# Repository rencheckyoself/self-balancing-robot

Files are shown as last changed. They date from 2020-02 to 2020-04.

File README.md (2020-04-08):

# Self Balancing Robot Project
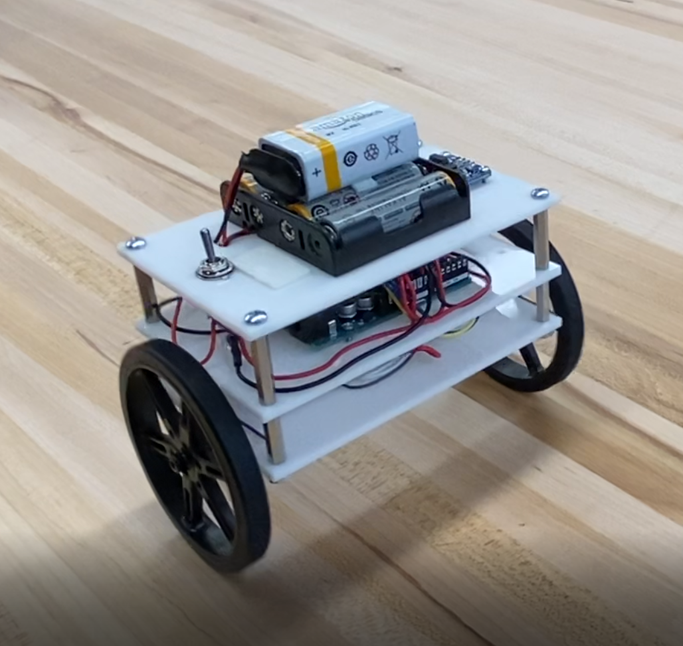
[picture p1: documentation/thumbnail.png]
thumbnail


This was a project to design and build a two-wheeled, self balancing robot that has a compact form factor. The challenge is that shorter the body design, the harder it is for the robot to easily maintain its balance. Since the feasibility of this system is not obvious, first the robot dynamics were solved and used to create a simulation of the system. This simulation was then used to inform the design and component selection process.

[Summary Video](https://www.youtube.com/watch?v=kY2ciNZqLZk)

This repository contains:
- A python script to the dynamics of the system and determine the equations of motion
- A ROS package that uses the equations of motion to simulate the self balancing robot
- Design files and BOM of the robot
- Arduino script to control the robot.

## How to use this repo:

If you want to use this repository to design your own self balancing robot or just recreate the iteration shown above, follow these steps:

**1) Run the  file `SelfBalancing_AllSymbolic.py`.**

Requires: python3, sympy, numpy, scipy, and pickle

This file will symbolically solve the Euler-Lagrange equations to derive the equations of motion that characterize a two wheeled, self balancing robot. This will generate a set of pickle files that are used to transfer the equations to the ROS simulation. This file takes about **30 min to fully run** due to the amount of symbols being processed, but your mileage may vary. If you would like to see the actual solutions, the raw Latex code is in the 'solutions.txt' file or you can run the `print_solutions.py` file.

See [derivations.pdf](documentation/derivations.pdf) in the documentation folder for more information on the system setup and derivation of the equations.

**2) Simulate the robot by launching `self_balance.launch`**

Requires: ROS Melodic

This will launch the simulation using the default settings used for the design files in this repo. Once loaded, call the `/start` service to start the simulation. You will need to update the `file_path_params.yaml` in the `simulate` node to update the locations of where to find pickle files you generated earlier.

Package Desciption:
  - `dynamics`: This package contains all of the files relevant to the computational component of the simulation. The `simulate` node uses an RK4 integration method combined with the symbolic equations of motion to compute the robot state for every time step. The robot state is then fed into a PID control scheme to compute the required motor torque to keep the robot upright following this control scheme shown below.

    - If you would like to customize the simulation to your own parameters, modify the `robot_params.yaml` file to simulate a different robot configuration. These parameters are best pulled from CAD files, see the included CAD mass properties images in the documentation directory for an example.

    - To modify the controller gains, change the values in the `controller_param.yaml` file.
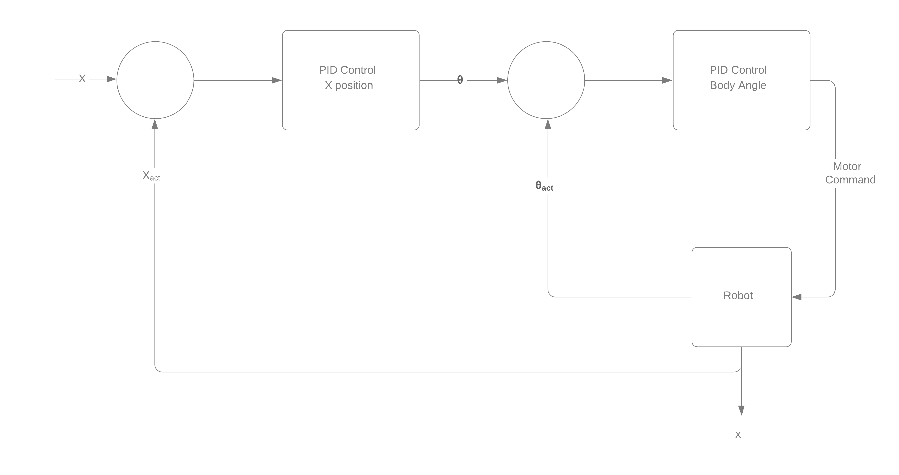
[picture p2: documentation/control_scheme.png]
ControlScheme
     

- `visualization`: This package contains all of the files relevant to the visual component of the simulation. The included launch file displays the `balance_bot.urdf.xacro` and is useful if you want to modify the existing model.

    - To use your own mesh, save an STL for your wheel and an STL for the robot body assembly and place them in the `meshes` directory. Either call your files the same name or update the file names inside of `balance_bot.urdf.xacro` to match your files.

**3) Build it!**

The files located in the `Prototyping` directory should be everything you need to build your own or use the insights discussed below to make your own modifications.

It contains:
 - CAD files
 - PDFs for laser cutting
 - Bill of materials
 - Wiring Diagram (shown below)
 - Arduino Source Code:   
 Required libraries:
 Adafruit BNO055,
 Adafruit Unified Sensor,
 EnableInterrupt by Mike Schwager,
 PID by Brett Beauregard,
 QuadratureEncoder by Cheng Saetern

There is an extra svg file called `motorSpacer.svg` that is meant for laser cutting an extra part not currently in the CAD. This piece goes between the motor and the bottom plate so that the encoder wires do not pinch the rotating magnet and stall the motors.

Currently the code does not actually incorporate the encoders to accomplish the position control component of the simulation.

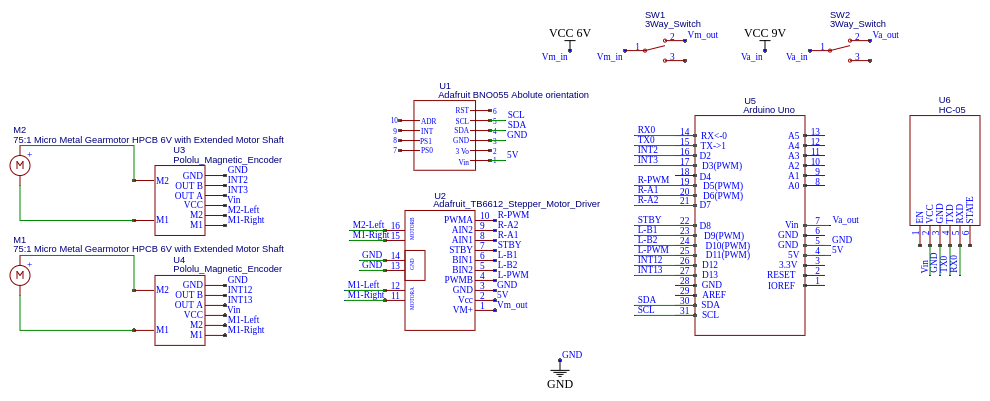
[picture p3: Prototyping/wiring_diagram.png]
WiringDiagram


## Lessons Learned

V2 is currently in-progress and the design will be largely the same but incorporating the changes based on the following insights:

1) The actual V1 build came out much heavier than anticipated, this can be attributed to not accounting for the components not in CAD (wires, nuts, screws, etc.) and the 9V battery. This was added late due to the 6V AA pack not being able to reliably power both the Arduino and the motors. 

2) The torques and speeds required for this design, are pushing these motors to their design limits. Therefore, any drop below their rated operating voltage of 6V really hurts their ability to output the required control.

3) The IMU used has onboard processing that provides easy access to an absolute position. Since the system is oscillating very quickly the 100Hz data stream may not be quick enough for to allow the motors enough time to react.

4) the IMU fell out of calibration after a few tests and caused the robot to try and balance to a non-vertical position.

5) There is some play in the wheel shaft to the gear box that allows the body to rotate a couple degrees without the motors spinning. Since the window of stable positions is only +/-6 degrees or so, this amount of play is not negligible.

Potential Solutions for V2:
 - Switch to aluminum standoff to save weight
 - Switch to an Arduino Nano and remove middle plate to save weight
 - Switch to 2S Lipo battery to save weight
 - integrate a 6V DC-DC regulator to power the motors
 - Incorporating encoder-based position control can help counteract the IMU calibration issues
 - Simulate V2 design a reevaluate motor selection based on required torques and wheel speeds
 - Slight increase of the body height to make the balancing easier and allow the control system more time to react.

## Future Plans

This repository is for an active project and a lot of insight was drawn from the first design.

Planned items:

- Integrate simulation functionality for different torques applied to each wheel. This will enable the simulation to turn and eventually follow waypoints.
- Construct a V2 robot that will be able to balance unteathered.
- Incorporate encoders into the V2 control scheme
- Control the physical robot to follow a set of waypoints in 3D space

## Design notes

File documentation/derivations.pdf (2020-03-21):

# Self Balancing Robot Derivations

### Michael Rencheck

### March 21, 2020

## 1 Problem Set Up

To solve the Euler-Lagrange equations, it is best to first define the frames and state vector that describe the problem and identify the transformations needed:

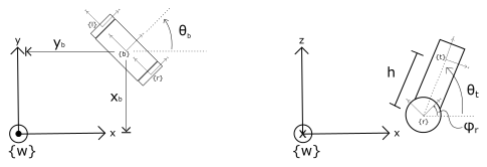
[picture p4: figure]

Figure 1: The frames used for the derivation

Frames:

w: world frame
b: robot base frame - centered between the wheels on the axis of rotation r: right wheel frame - centered on the wheel
l: left wheel frame - centered on the wheel
t: center of mass frame - located line with the base frame

Parameters:

xb: robot x-position
yb: robot y-position
θb: robot heading angle
θt
: robot body angle
φr: right wheel angle
φl

: left wheel angle
r: wheel radius
ht

: distance from rotation point to the center of mass D: distance between the two wheels

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

Find the kinetic energy of each link:

KEtot = KEr + KEl + KEt

KEr =

1
2

∗ Vr

T
∗ Gwheel ∗ Vr

KEl =

1
2

∗ Vl

T
∗ Gwheel ∗ Vl

KEt =

1
2

∗ Vt

T
∗ Gbody ∗ Vt

Where:
V: is a 6Vector twist
G: is a spatial inertia matrix
m: is mass of the respective body
I: is the moment of inertia about a principle axis

Vx = T

−1

wx ∗ T˙
wx

Gx =

mx | 0 | 0 | 0 | 0 | 0
0 | mx | 0 | 0 | 0 | 0
0 | 0 | mx | 0 | 0 | 0
0 | 0 | 0 | Ixx | 0 | 0
0 | 0 | 0 | 0 | Iyy | 0
0 | 0 | 0 | 0 | 0 | Izz

Find the Potential Energy of each link:

P Etot = P Er + P El + P Et

P Er = 0

P El = 0

P Et = (mtgh)sin(θt)

Define the constraint equations¹ :

λ =

"
λ1
λ2

∇φ =

"
1 0 0 r ∗ cos(θb) r ∗ cos(θb) 0

0 1 0 r ∗ sin(θb) r ∗ sin(θb) 0#

Last define the external force vector:

1For more details, see Robotic Manipulation, Murry, Li, Sastry pg. 272

Fext =

0
0
0

τmotor

τmotor
0

Finally solve the systems of equations for q¨ and λ:

dL
dq˙

−

dL
dq = Fext + λ∇φ

φ¨ =

d
dt(∇φ ∗ q˙)

See the included txt for the raw latex code of the solutions. This output was generated using the included python code.

A couple notation changes in the txt file: subscript w: wheel subscript b: body t variables: θ p variables: φ
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

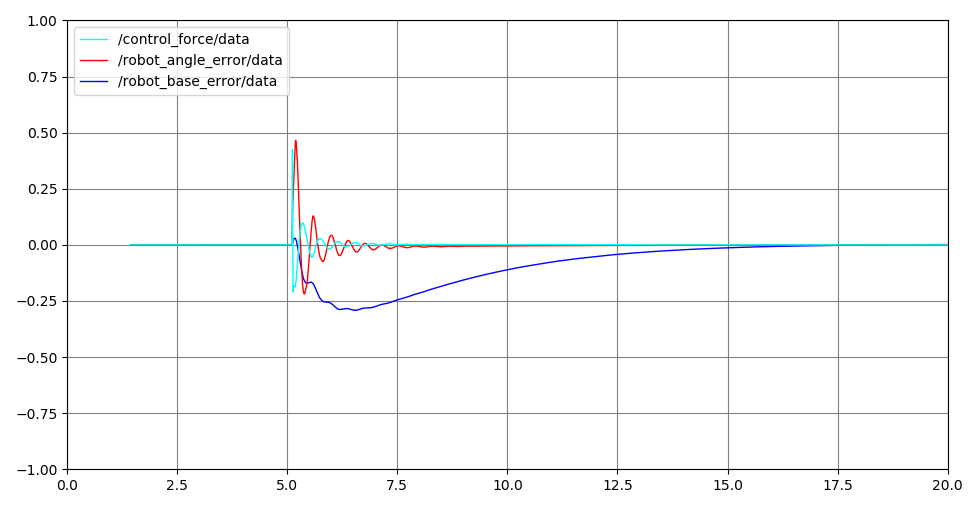
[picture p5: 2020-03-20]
documentation/simulatiuonresults.png

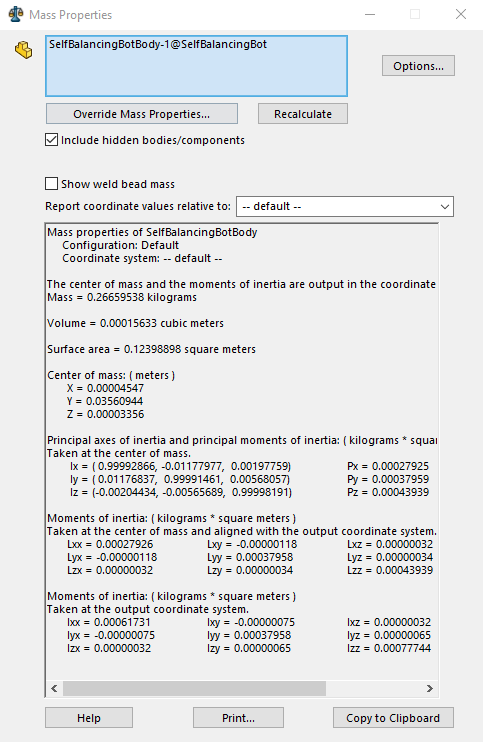
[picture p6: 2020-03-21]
documentation/V1 Body Properties.png

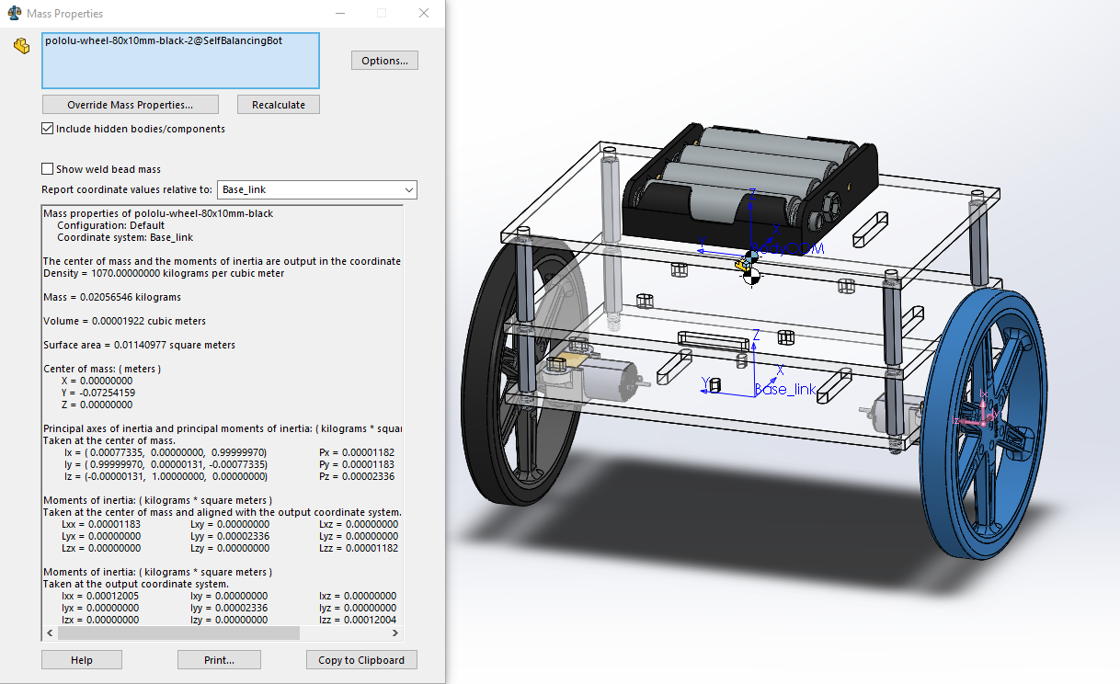
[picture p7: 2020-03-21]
documentation/WheelInertia.png

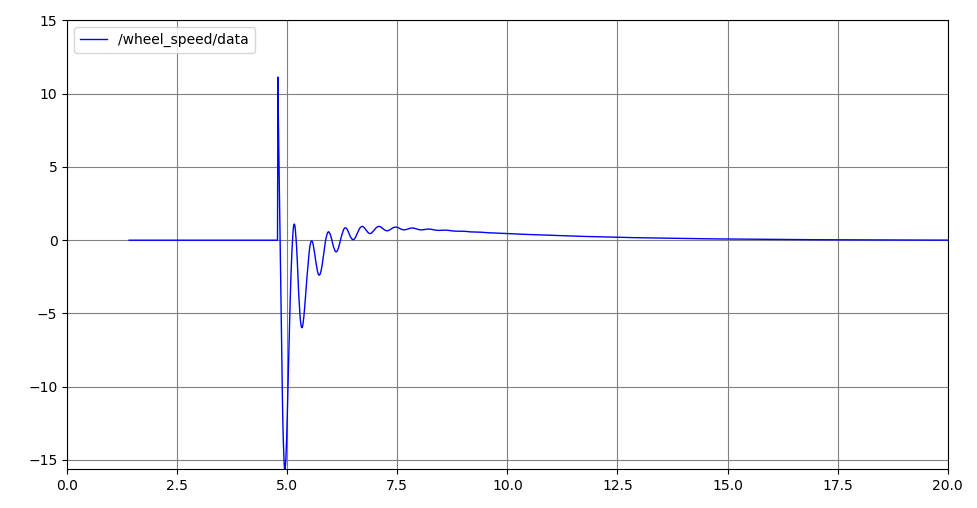
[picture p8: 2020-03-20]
documentation/wheel_speed.png

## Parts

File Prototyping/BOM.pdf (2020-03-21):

| Link | Quantity
Body | 1/8" Acryllic
Motors | https://www.pololu.com/product/3074 | 2
Motor Mount | https://www.pololu.com/product/989 | 2
Wheels | https://www.pololu.com/product/1430 | 2
Motor Driver | https://www.adafruit.com/product/2448 | 1
Encoders | https://www.pololu.com/product/3081 | 2
IMU | https://www.adafruit.com/product/2472 | 1
AA Battery Holder https://www.amazon.com/LAMPVPATH-Battery-Holder-Leads-Wires/dp/B07T7MTRZX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 1
9V Battery Connectorhttps://www.amazon.com/BBTO-Battery-Connector-Cable-Connection/dp/B0779ZSNS3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 1
Toggle Switch | https://www.amazon.com/yueton-Terminals-Position-Toggle-Switch/dp/B013DZB6CO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 1
Arduino Uno | https://www.amazon.com/ARDUINO-A000073-ATMEGA328-Original-Version/dp/B007R9TUJE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 1
Standoffs | https://www.mcmaster.com/91075a117 | 4
Standoffs | https://www.mcmaster.com/91075a115 | 4
Screws | #2/56 for PCBs & #6/32 | Various
Nuts | #2/56 for PCBs & #6/32 | Various
Lock Washers | #2/56 for PCBs & #6/32 | Various

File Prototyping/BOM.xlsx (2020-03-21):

 | Link | Quantity | Notes
Body | 1/8" Acryllic
Motors | https://www.pololu.com/product/3074 | 2
Motor Mount | https://www.pololu.com/product/989 | 2
Wheels | https://www.pololu.com/product/1430 | 2
Motor Driver | https://www.adafruit.com/product/2448 | 1 | PWM for velocity control
Encoders | https://www.pololu.com/product/3081 | 2
IMU | https://www.adafruit.com/product/2472 | 1 | May not be needed if the camera has the IMU
AA Battery Holder | https://www.amazon.com/LAMPVPATH-Battery-Holder-Leads-Wires/dp/B07T7MTRZX | 1
9V Battery Connector | https://www.amazon.com/BBTO-Battery-Connector-Cable-Connection/dp/B0779ZSNS3?s=industrial | 1
Toggle Switch | https://www.amazon.com/yueton-Terminals-Position-Toggle-Switch/dp/B013DZB6CO?s=industrial | 1
Arduino Uno | https://www.amazon.com/ARDUINO-A000073-ATMEGA328-Original-Version/dp/B007R9TUJE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 | 1
Standoffs | https://www.mcmaster.com/91075a117 | 4
Standoffs | https://www.mcmaster.com/91075a115 | 4
Screws | #2/56 for PCBs & #6/32 | Various
Nuts | #2/56 for PCBs & #6/32 | Various
Lock Washers | #2/56 for PCBs & #6/32 | Various

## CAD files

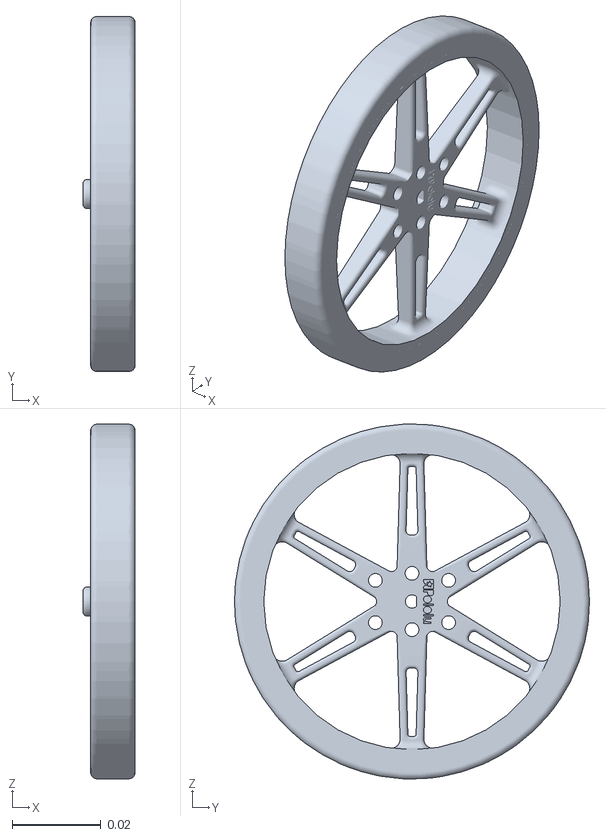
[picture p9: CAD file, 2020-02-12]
src/visualization/meshes/Wheel.STL
0.0117 x 0.08 x 0.0799

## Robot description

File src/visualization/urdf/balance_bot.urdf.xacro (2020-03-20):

<?xml version="1.0"?>
<robot xmlns:xacro="http://www.ros.org/wiki/xacro" name="balance_bot">


  <!-- Load in parameters from the YAML file -->
  <xacro:property name="props" value="${load_yaml('$(find dynamics)/config/robot_params.yaml')}"/>

  <xacro:property name="wheel_radius" value="${props['wheel_radius']}"/>
  <xacro:property name="wheel_base" value="${props['body_wheel_base']}"/>

  <xacro:property name="body_width" value="${props['body_width']}"/>
  <xacro:property name="body_height" value="${props['body_height']}"/>
  <xacro:property name="body_thickness" value="${props['body_thickness']}"/>
  <xacro:property name="body_com_height" value="${props['body_com_height']}"/>

  <xacro:property name="motor_height" value="0.0115"/> <!-- distance between wheel rotation axis and bottom plate-->
  <xacro:property name="mid_tier" value="0.0191"/> <!-- distance between mid plate and bottom plate-->
  <xacro:property name="top_tier" value="0.0254"/> <!-- distance between mid plate and top plate-->
  <xacro:property name="motor_shaft" value="0.00907"/> <!-- length of the motor_shaft -->

  <material name="smokey">
    <color rgba=".1 .1 .1 1"/>
  </material>

  <material name="wheel">
    <color rgba=".5 .5 .5 .5"/>
  </material>

  <material name="invisible">
    <color rgba="0 0 0 0"/>
  </material>

  <!-- Macro to load a part with a mesh -->
  <xacro:macro name="body_link_mesh" params="name lxyz lrpy mat meshfile meshscale jxyz jrpy">
    <link name="${name}">
      <visual>
        <origin rpy="${lrpy}" xyz="${lxyz}" />
        <geometry>
          <mesh filename="${meshfile}" scale="${meshscale}"/>
        </geometry>
        <material name="${mat}"/>
      </visual>
    </link>

    <joint name= "${name}_joint" type="fixed">
      <origin xyz="${jxyz}" rpy="${jrpy}" />
      <parent link="moving_link"/>
      <child link="${name}" />
    </joint>
  </xacro:macro>

  <xacro:macro name="wheel_link_mesh" params="name lxyz lrpy mat meshfile meshscale jxyz jrpy">
    <link name="${name}">
      <visual>
        <origin rpy="${lrpy}" xyz="${lxyz}" />
        <geometry>
          <mesh filename="${meshfile}" scale="${meshscale}"/>
        </geometry>
        <material name="${mat}"/>
      </visual>
    </link>

    <joint name= "${name}_axle" type="continuous">
      <origin xyz="${jxyz}" rpy="${jrpy}" />
      <parent link="base_link"/>
      <child link="${name}" />
      <axis xyz = "0 -1 0"/>
    </joint>
  </xacro:macro>

  <!-- The base link of the robot center between the two wheels directly below the COM of the body -->
  <link name="base_link" >
    <visual>
      <geometry>
        <sphere radius=".0025" />
      </geometry>
      <material name="black">
        <color rgba="0 0 0 1" />
      </material>
      <origin rpy="0 0 0" xyz="0 0 ${wheel_radius}"/>
    </visual>
  </link>

  <link name="moving_link">
    <visual>
      <geometry>
        <sphere radius=".0025" />
      </geometry>
      <material name="black"/>
      <origin xyz="0 0 ${body_com_height}" rpy="0 0 0"/>
    </visual>
  </link>

  <joint name="body_joint" type="continuous">
    <origin xyz="0 0 ${wheel_radius}" rpy="0 ${-pi/2} ${pi}" />
    <parent link="base_link"/>
    <child link="moving_link" />
    <axis xyz="0 1 0"/>
  </joint>

  <xacro:body_link_mesh name="body_mesh" mat="smokey" lxyz="${-body_thickness/2} ${-body_width/2 - motor_shaft} ${-motor_height/2}" lrpy="0 0 0" meshfile="package://visualization/meshes/SelfBalancingBotBody.STL" meshscale="1 1 1" jxyz="0 0 0" jrpy="0 0 0"/>

  <xacro:wheel_link_mesh name="left_wheel" mat="wheel" lxyz="${wheel_radius} ${body_width/2} ${-wheel_radius}" lrpy="0 0 ${pi/2}" meshfile="package://visualization/meshes/Wheel.STL" meshscale="1 1 1" jxyz="0 0 ${wheel_radius}" jrpy="0 0 0"/>

  <xacro:wheel_link_mesh name="right_wheel" mat="wheel" lxyz="${-wheel_radius} ${-(body_width/2)} ${-wheel_radius}" lrpy="0 0 ${-pi/2}" meshfile="package://visualization/meshes/Wheel.STL" meshscale="1 1 1" jxyz="0 0 ${wheel_radius}" jrpy="0 0 0"/>

</robot>

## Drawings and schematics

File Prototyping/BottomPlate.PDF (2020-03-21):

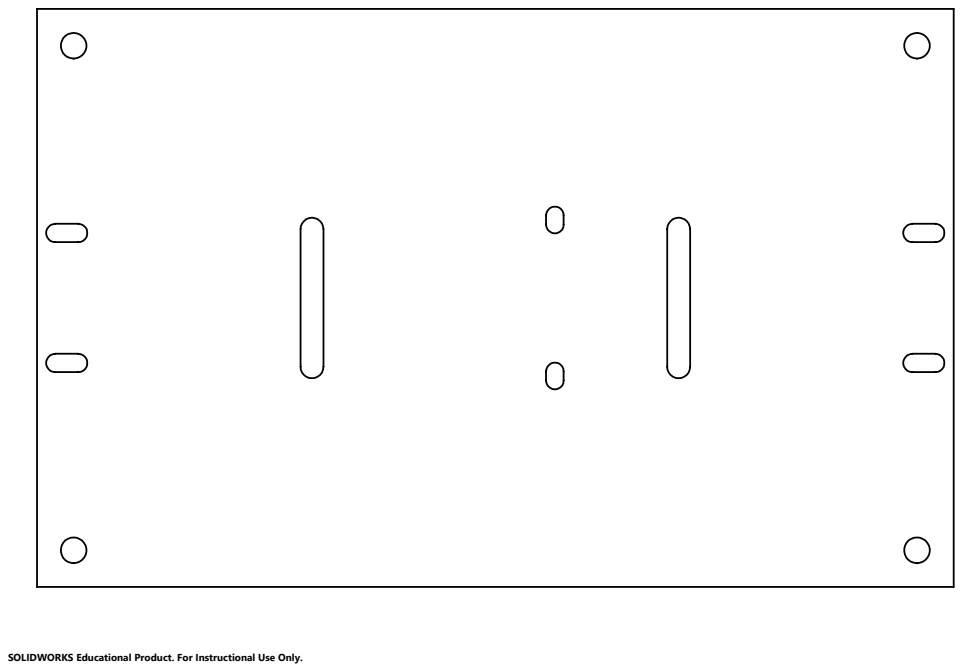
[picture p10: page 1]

SOLIDWORKS Educational Product. For Instructional Use Only.

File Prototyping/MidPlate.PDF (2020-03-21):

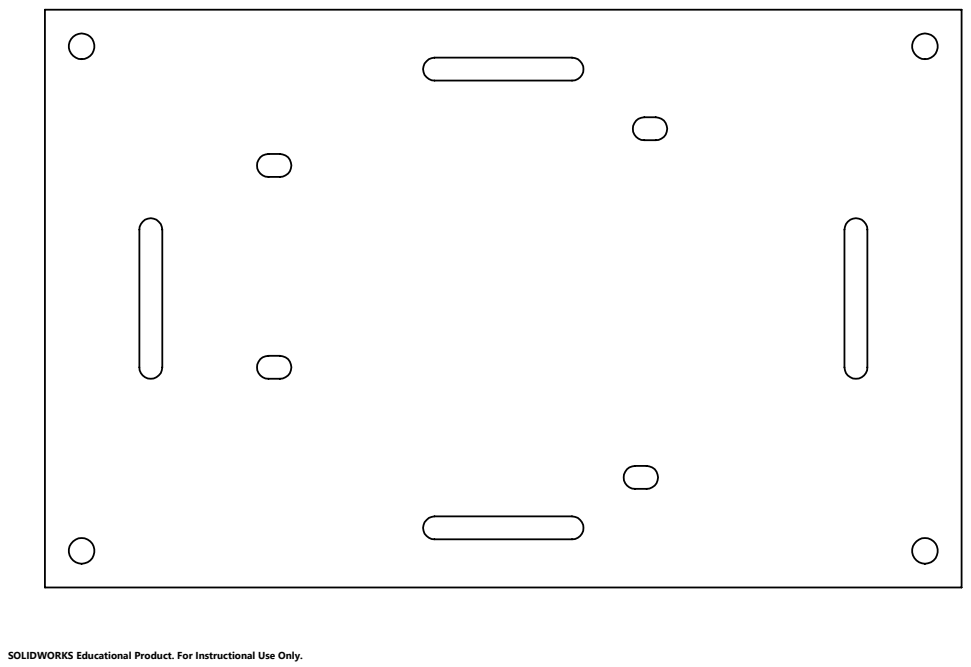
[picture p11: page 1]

SOLIDWORKS Educational Product. For Instructional Use Only.

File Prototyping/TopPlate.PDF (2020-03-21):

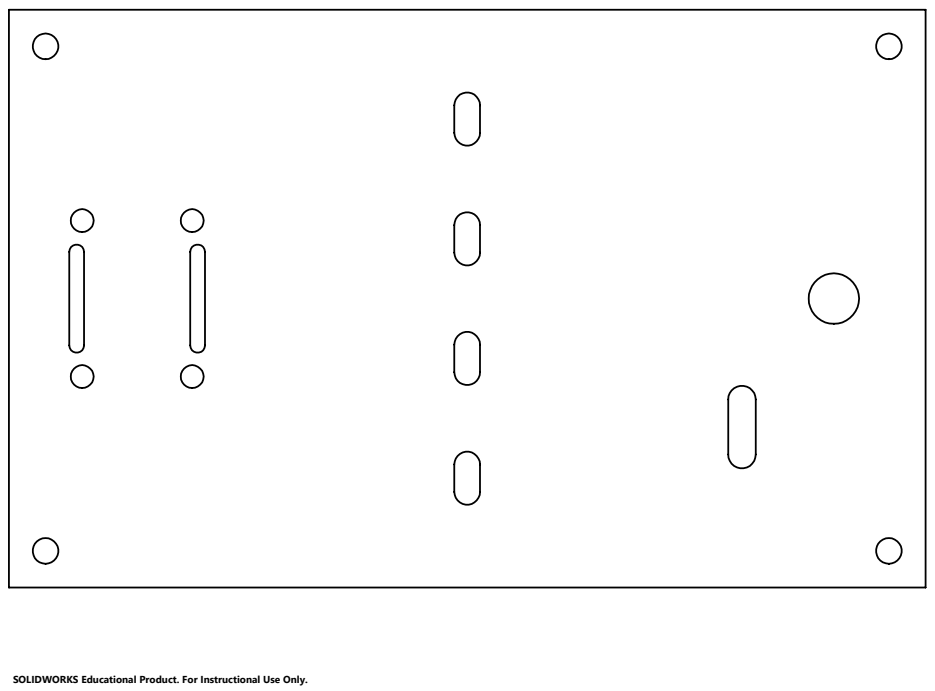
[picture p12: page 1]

SOLIDWORKS Educational Product. For Instructional Use Only.

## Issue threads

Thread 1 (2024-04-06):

About the SolverEom and service start

AkhilAsok11, 2024-04-06:
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

Even after running the solverEOM for 3 hours it just shows like this. While trying to use rosservice call/start it shows an error "This service is not available". Sols.pickle is also not found. Can you please help me resolve this issue, the college submission date is so close.

rencheckyoself, 2024-04-06:
So all your problems are related to solverEOM never finishing. The start service doesn't exist because the node the offers if crashes (top-right pane). This is because the `sols.pickle` file isn't found because step 1 never finishes.

Step 1 does not require ROS so just run the python script by running: `python3 SelfBalancing_AllSymbolic.py`

AkhilAsok11, 2024-04-06:
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
 Now when I try to run the solvereom it shows like this. I'm having a doubt about the hams.pickle file. While trying to run the other Python codes there was an error since the pickle extension was not installed in vs code. when I installed Pickle using vs code a hams.pickle was created automatically. Is this pickle file and the hams.pickle file that you mentioned are the same?

AkhilAsok11, 2024-04-06:
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
Still after 2 hours, there is no change.

rencheckyoself, 2024-04-06:
Yea, the `SelfBalancing_AllSymbolic.py` will generate two pickle files. Ham.pickle and Sols.pickle. These are the equations of motion that represent the self-balancing robot. Pickle is a package that should be bundled directly with Python.

I pulled the code to my machine and tried to run it and am getting the same behavior as you which leads me to think it's an issue with the newer versions of these packages not being compatible with my code. The program freezes when it gets to this line:
https://github.com/rencheckyoself/self-balancing-robot/blob/a0bc76c4998d2fcb530cac204b792cd91f3da6be/SolveEOM/SelfBalancing_AllSymbolic.py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

My first guess at the issue is there's something up with the inputs to the `sym.solve()` function due to an update they've made since this was written 4 years ago. So you can dig into the Sympy documentation and debug what's causing the issue.

Something else that came to mind is making sure your computer isn't going to sleep/suspending/blanking the screen during that 2hr period. The one I tried it on did so that might also be the cause of it never finishing. I just started running it again and the program seems to be running because it's fully utilizing one of my CPU cores.

Another solution would be to install the version of Python 3 and the packages that would've existed in early 2020 and run it with them instead of whatever the current version is. Or even just make a bootable USB of Ubuntu 18 and try running it on that.

rencheckyoself, 2024-04-06:
Also the program does seem to be generating a Ham.pickle file. It will get saved to the directory your terminal is set to when you run the SelfBalancing script. You can modify the `print_solutions.py` file to read and print the contents of `Ham.pickle` to verify the output is correct.

AkhilAsok11, 2024-04-06:
While running this solvereom my screen was always on even without blanking the screen. I will try to run the program using a bootable USB of Ubuntu 18. since I'm new to programming and ros I may not have the luxury of time to debug the sympy documentation. Is it possible to self-balance the robot without using the sovereom files? Can we use only pid files to self-balance the robot? Do you have the requirement file for this project?

rencheckyoself, 2024-04-06:
I'm not sure what you mean by "requirement file". Step 1 computes the equations of motion for a self-balancing robot, but leaves everything in symbolic form. The pickle files are used to serialize those equations and save them for future use. Step 2 loads those pickle files and then uses those equations with an integrator to compute the motion of the drone. It's only in ROS as a tool for visualizing what the robot is doing. You can't just use the PID files alone because it needs the equations of motion from step 1.

I was digging through the repo and found that I saved the solutions at some point in a text file: https://github.com/rencheckyoself/self-balancing-robot/blob/master/documentation/solutions.txt
Github doesn't allow pushing pickle files (or they didn't at the time) as a security precaution so I had to just do a text file.

You could use these to hard code the EOM in the ros node and eliminate the need for step 1. Here is where the `Sols.pickle` gets loaded:
https://github.com/rencheckyoself/self-balancing-robot/blob/master/src/dynamics/nodes/simulate#L203C1-L223C84
Instead of using sympy to create the usable equations you could write 6 python functions that each take  `cur_loc`  as an input and returns the state value the fuction corresponds to. Something like:
```
def EOM_lxb(cur_loc):
     return <hardcoded function for xb>
```
Then you would need 5 more functions for the other 5 pieces of the state.

Then put those 6 functions into the `self.eom_for_state` variable instead of the the EOMl_* variables here: https://github.com/rencheckyoself/self-balancing-robot/blob/master/src/dynamics/nodes/simulate#L223

AkhilAsok11, 2024-04-08:
Tomorrow is my second last presentation of the project. Can I clarify some things about this project? Is the  SelfBalancing_AllSymbolic.py file used to find the position and angle of the robot? EULER-LEGRANGE & HAMILTONIAN EQUATIONS are used in this to find the position and angle right? And after getting the angle and position it will be given to the PID controller to calculate the amount of torque that should to the controller. Is this the process that is happening through the Python files? Please do answer my queries. Now I'm trying to use cur_loc as you mentioned before. As I'm new to coding, I'm just thinking how to add this code properly
   "def EOM_lxb(cur_loc):
        return <hardcoded function for xb>"

AkhilAsok11, 2024-04-08:
def EOM_lxb(cur_loc):
    return (
        (0.5 * rw) /
        (Iyyb * Iyyw + 2.0 * Iyyb * mb * rw**2 + 4.0 * Iyyb * mw * rw**2 + Iyyw * hcom**2 * mb +
         2.0 * hcom**2 * mb**2 * rw**2 * cos(cur_loc[10])**2 +
         4.0 * hcom**2 * mb * mw * rw**2)
    ) * (
        (
            4.0 * hcom * mb * rw * (Iyyb + hcom**2 * mb) * (
                cur_loc[5]**2 * sin(cur_loc[4]) * cos(cur_loc[10]) +
                2.0 * cur_loc[5] * cur_loc[11] * sin(cur_loc[10]) * cos(cur_loc[4]) +
                cur_loc[11]**2 * sin(cur_loc[4]) * cos(cur_loc[10])
            ) * sin(cur_loc[4]) * cos(cur_loc[4]) +
            4.0 * hcom * mb * rw * (Iyyb + hcom**2 * mb) * (
                cur_loc[5]**2 * cos(cur_loc[4]) * cos(cur_loc[10]) -
                2.0 * cur_loc[5] * cur_loc[11] * sin(cur_loc[4]) * sin(cur_loc[10]) +
                cur_loc[11]**2 * cos(cur_loc[4]) * cos(cur_loc[10])
            ) * cos(cur_loc[4])**2 -
            4.0 * hcom * mb * rw * (
                - Izzb * cur_loc[5]**2 * sin(cur_loc[10]) +
                g * hcom * mb +
                hcom**2 * mb * cur_loc[5]**2 * sin(cur_loc[10])
            ) * sin(cur_loc[10]) * cos(cur_loc[4]) * cos(cur_loc[10]) +
            4.0 * rw**2 * cur_loc[5] * (pld + prd) * (
                Iyyb * mb + 2.0 * Iyyb * mw + hcom**2 * mb**2 * cos(cur_loc[10])**2 +
                2.0 * hcom**2 * mb * mw
            ) * sin(cur_loc[4]) * cos(cur_loc[4])**2 +
            2.0 * cur_loc[5] * (pld + prd) * (
                Iyyb * Iyyw + Iyyw * hcom**2 * mb - 2.0 * hcom**2 * mb**2 * rw**2 *
                sin(cur_loc[4])**4 * sin(cur_loc[10])**2 -
                2.0 * hcom**2 * mb**2 * rw**2 * sin(cur_loc[4])**2 * sin(cur_loc[10])**2 *
                cos(cur_loc[4])**2 +
                2.0 * rw**2 * (Iyyb + hcom**2 * mb) * (mb + 2.0 * mw) * sin(cur_loc[4])**2
            )
        ) * sin(cur_loc[4]) -
        (2.0 * Fw - Izzw * cur_loc[5]**2 * sin(2.0 * pl)) * (Iyyb + hcom**2 * mb) * cos(cur_loc[4]) -
        (2.0 * Fw - Izzw * cur_loc[5]**2 * sin(2.0 * pr)) * (Iyyb + hcom**2 * mb) * cos(cur_loc[4])
    )
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
rencheckyoself, 2024-04-08:
Yea, I think you have the correct understanding for what the package is doing and yes that looks like what I had in mind for the code change.

AkhilAsok11, 2024-04-08:
While searching on Google I saw the usage of IMU sensor plugins to determine the angle of the robot. Are we using this plugin in this project? The Euler-Lagrange equations are used to find the position and angle right. So why are we using Hamilton equations? Have we used the dynamic model of the robot in the SelfBalancing_AllSymbolic.py file. And if it's used what is the benefit or need for the dynamic model?

rencheckyoself, 2024-04-08:
No it's not using that plugin. Yes, the EL equations are being used to compute the state of the robot. Since we are using an integrator to propagate the state, the Hamilton equations can be used to evaluate the quality of the simulation and help determine if there was an error in the dynamic model. In short, they are a debugging tool.

SelfBalancing_AllSymbolic.py solves for the dynamic model, then the ros node uses it with a PID controller to simulate the robot. Since the equations were solved symbolically you can easily substitute in different properties such as mass, inertias, wheel size, axel distance, starting position, etc. Then we can observe the required torques, motor speeds, and motor accelerations required to control the robot and select a motor that is capable of matching this performance for the build.

AkhilAsok11, 2024-04-09:
The dynamic model is solved through the SelfBalancing_AllSymbolic.py file to obtain the equations of position and angle right? My doubt is that are we creating the PID controller  using the equations of position and angle that we obtained by solving the dynamic model. Once we have the angle and position errors, do we input it directly into the PID controller to balance the robot? Or, do we incorporate this error into the position and angle equations to calculate a value, which is then fed into the PID controller to determine the correct motor torque? How do we determine the error in position and angle of the robot without employing sensors or plugins?

AkhilAsok11, 2024-04-10:
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

While hardcoding this mb,rw, Iyyw, etc.. was not defined. i tried to define it but I can't understand what is F_{w} in this code. Can you please define F_{w}.

rencheckyoself, 2024-04-10:
https://github.com/rencheckyoself/self-balancing-robot/blob/master/src/dynamics/nodes/simulate#L176C1-L199C115

You'll have to either change the class variables to match your hard coded equations or vice versa.

AkhilAsok11, 2024-04-10:
Ya, I changed all the variables in the hard code like m_b to  m_body , h_{com} to COMz, etc... but only for the variable  F_{w} I don't know what to give.

rencheckyoself, 2024-04-10:
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

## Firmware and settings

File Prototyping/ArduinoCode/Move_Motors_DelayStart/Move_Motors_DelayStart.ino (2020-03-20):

#include <EEPROM.h>
#include <Wire.h>

#include <QuadratureEncoder.h>

#include <Adafruit_Sensor.h>
#include <Adafruit_BNO055.h>
#include <utility/imumaths.h>

#include <PID_v1.h>

#include "Setup.h"
#include "imu_utility.hpp"
#include "motor_driver_utility.hpp"

#define READ_ANGLE euler.y()


// initialize encoders
static Encoders leftEncoder(MOTOR_LEFT_ENC1, MOTOR_LEFT_ENC2);
static Encoders rightEncoder(MOTOR_RIGHT_ENC1, MOTOR_RIGHT_ENC2);

static const int counts_per_rev = 900; // revolutions of the wheel
static int cnt = 1;

static volatile int left_enc_cnt = 0, right_enc_cnt = 0;

static int dirMotors, posLMotor, posRMotor, selectMotors;
static int dirLMotor, dirRMotor;

static Adafruit_BNO055 bno = Adafruit_BNO055(55, 0x28);

static double Setpoint, Input, Output;
static double Kp=40, Ki=0, Kd=90;
static PID anglePID(&Input, &Output, &Setpoint, Kp, Ki, Kd, P_ON_E, DIRECT);

static float body_ang=0, abs_ba = 0;
// Function Prototypes
void loadCalibaration(void);

void setup() {

  Serial.begin(115200);
  Serial.println("Orientation Sensor Test"); Serial.println("");

  /* Initialize the sensor */
  if (!bno.begin())
  {
      Serial.print("Ooops, no BNO055 detected ... Check your wiring or I2C ADDR!");
      while (1);
  }

  loadCalibaration();
  Setpoint = HOME_ANGLE;
  anglePID.SetSampleTime(1); // 200Hz
  anglePID.SetOutputLimits(-255, 255); //PWM Output
  anglePID.SetMode(AUTOMATIC);
  
  //initialize DC Motors
  pinMode(MOTOR_RIGHT_PWM,OUTPUT);
  pinMode(MOTOR_RIGHT_1,OUTPUT);
  pinMode(MOTOR_RIGHT_2,OUTPUT);
  pinMode(MOTOR_STANDBY,OUTPUT);
  pinMode(MOTOR_LEFT_PWM,OUTPUT);
  pinMode(MOTOR_LEFT_1,OUTPUT);
  pinMode(MOTOR_LEFT_2,OUTPUT);

  // Enable motors
  digitalWrite(MOTOR_STANDBY,HIGH);
  
  Serial.println("DC Motors Initialized");

  delay(1000);
  
  Serial.println("Ready!");
}


void loop() {
  // Possible vector values can be:
  // - VECTOR_ACCELEROMETER - m/s^2
  // - VECTOR_MAGNETOMETER  - uT
  // - VECTOR_GYROSCOPE     - rad/s
  // - VECTOR_EULER         - degrees
  // - VECTOR_LINEARACCEL   - m/s^2
  // - VECTOR_GRAVITY       - m/s^2
  
  imu::Vector<3> euler = bno.getVector(Adafruit_BNO055::VECTOR_EULER);
  
  euler = bno.getVector(Adafruit_BNO055::VECTOR_EULER);
  body_ang = READ_ANGLE;
  Input = body_ang;
  
  anglePID.Compute();
  
  Serial.print(body_ang);
  Serial.print(" ");
  
  if(body_ang >= HOME_ANGLE)
  {
    moveMotorBKD(int(Output)*-1);
    Serial.println(int(Output));
  }
  
  else if(body_ang < HOME_ANGLE)
  {
    moveMotorFWD(int(Output));
    Serial.println(int(Output));
  }   
}


/// \brief Load in Calibration data
///
void loadCalibaration(void)
{
  int eeAddress = 0;
  long bnoID;
  bool foundCalib = false;

  EEPROM.get(eeAddress, bnoID);

  adafruit_bno055_offsets_t calibrationData;
  sensor_t sensor;

  /*
  *  Look for the sensor's unique ID at the beginning oF EEPROM.
  *  This isn't foolproof, but it's better than nothing.
  */
  bno.getSensor(&sensor);  
  if (bnoID != sensor.sensor_id)
  {
      Serial.println("\nNo Calibration Data for this sensor exists in EEPROM");
      delay(500);
  }
  else
  {
//      Serial.println("\nFound Calibration for this sensor in EEPROM.");
      eeAddress += sizeof(long);
      EEPROM.get(eeAddress, calibrationData);

      displaySensorOffsets(calibrationData);

//      Serial.println("\n\nRestoring Calibration data to the BNO055...");
      bno.setSensorOffsets(calibrationData);

//      Serial.println("\n\nCalibration data loaded into BNO055");
      foundCalib = true;
  }

  delay(1000);

  /* Crystal must be configured AFTER loading calibration data into BNO055. */
  bno.setExtCrystalUse(true);

//  sensors_event_t event;
//  bno.getEvent(&event);
//
//  if (foundCalib){
//        Serial.println("Move sensor slightly to calibrate magnetometers");
//        while (!bno.isFullyCalibrated())
//        {
//            bno.getEvent(&event);
//            delay(BNO055_SAMPLERATE_DELAY_MS);
//        }
//    }
//    else
//    {
//        Serial.println("Please Calibrate Sensor: ");
//        while (!bno.isFullyCalibrated())
//        {
//            bno.getEvent(&event);
//
//            Serial.print("X: ");
//            Serial.print(event.orientation.x, 4);
//            Serial.print("\tY: ");
//            Serial.print(event.orientation.y, 4);
//            Serial.print("\tZ: ");
//            Serial.print(event.orientation.z, 4);
//
//            /* Optional: Display calibration status */
//            displayCalStatus(&bno);
//
//            /* New line for the next sample */
//            Serial.println("");
//
//            /* Wait the specified delay before requesting new data */
//            delay(BNO055_SAMPLERATE_DELAY_MS);
//        }
//    }
//    
//    Serial.println("\nFully calibrated!");
//    Serial.println("--------------------------------");
//    Serial.println("Calibration Results: ");
//    adafruit_bno055_offsets_t newCalib;
//    bno.getSensorOffsets(newCalib);
//    displaySensorOffsets(newCalib);
//
//    Serial.println("\n\nStoring calibration data to EEPROM...");
//
//    eeAddress = 0;
//    bno.getSensor(&sensor);
//    bnoID = sensor.sensor_id;
//
//    EEPROM.put(eeAddress, bnoID);
//
//    eeAddress += sizeof(long);
//    EEPROM.put(eeAddress, newCalib);
//    Serial.println("Data stored to EEPROM.");
//
//    Serial.println("\n--------------------------------\n");
//    delay(500);
}

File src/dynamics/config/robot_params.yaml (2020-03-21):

# All units are in m and kg

init_state: [0, 0, 0, 0, 0, 0, 0, 0, 0, 0, 1.471, 0] # the initial starting position of the robot. Syntax: (xb, xb_dot, yb, yb_dot, tb, tb_dot, pr, pr_dot, pl, pl_dot, tt, tt_dot)

wheel_radius: 0.04 # Radius of the wheels
wheel_mass: 0.020 # mass of a wheel

wheel_Ixx: 0.00012005 # the Ixx component of the wheel intertia
wheel_Iyy: 0.00002336 # the Iyy component of the wheel inertia
wheel_Izz: 0.00012004 # the Izz component of the wheel inertia

body_width: 0.13 # y distance of the body
body_height: 0.28264 # z distance of the body
body_thickness: 0.08 # x distance of the body

body_wheel_base: 0.13554 # Distance between the wheels centers
body_com_height: 0.0437 # Height to the COM of the body from the base link
body_mass: 0.25 # The mass of the body assembly

body_Ixx: 0.00095037 # the Ixx component of the body intertia
body_Iyy: 0.00079066 # the Iyy component of the body inertia
body_Izz: 0.00038029 # the Izz component of the body inertia

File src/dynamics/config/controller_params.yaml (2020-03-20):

frequency: 100 # Hz, sets computation rate

kp_ang: 0.38 # proportional gain for body angle, must be positive
ki_ang: 0.045 # integral gain for body angle, must be positive
kd_ang: 0.035 # derivative gain for body angle, must be positive

kp_x: 0.018 # proportional gain for body x position, must be positive
ki_x: 0 #0.005 # integral gain for body x position, must be positive
kd_x: 0.37 #0.04 # derivative gain for body x position, must be positive

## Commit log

2020-01-29 3D case working with no control
2020-02-04 Beginning Conversion to ROS Package
    [controller_params.yaml, robot_params.yaml]
2020-02-04 Successfully publishing wheel positions
    [robot_params.yaml]
2020-02-08 updated config files
    [robot_params.yaml]
2020-02-09 Successful & tested reconfiguration of simulate node. Started on urdf construction.
    [BottomPlate.STL, LongStandoff.STL, MidPlate.STL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]
2020-02-09 partial_construction of urdf
    [BottomPlate.STL, LongStandoff.STL, MidPlate.STL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]
2020-02-12 Completed Integration for Unforced robot. Need to implement PID controller class
    [BottomPlate.STL, LongStandoff.STL, MidPlate.STL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]
2020-02-12 Successful PID Control integration. Next step is to add services to modify parameters while sim is running.
    [controller_params.yaml]
2020-02-19 Successfully staying at 0,0
    [controller_params.yaml]
2020-02-21 Controller tinkering
    [controller_params.yaml]
2020-03-02 Fairly well tuned system. Need to verify err integration handling
    [controller_params.yaml]
2020-03-02 better tunings
    [controller_params.yaml]
2020-03-09 Added Arduino code (untested) and some documentation
2020-03-20 Documentation updates
    [robot_params.yaml]
2020-03-20 Updated sim to fix visulaization bug and added start service
    [balance_bot.urdf.xacro, controller_params.yaml]
2020-03-21 add more params to config files. repo organization, readme updates, documentation
    [BOM.xlsx, robot_params.yaml]
